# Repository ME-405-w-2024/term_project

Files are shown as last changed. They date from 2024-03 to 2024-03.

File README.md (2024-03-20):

# Term Project for ME405 at California Polytechnic University

## Contributors: Kevin Jung, Aidan Schwing, Noah Fitzgerald

Documentation available at: https://me-405-w-2024.github.io/term_project/

---

## Introduction
The code and CAD files present in this repository serve as reference for a fixed position, single-axis mechanism intended to shoot NERF RIVAL balls of approximately 1" diameter. This robot participated in a duel-style competition where two teams with similarly designed mechanisms competed to shoot the opposing team as quickly as possible. Robots were required to begin facing backwards, rotate 180 degrees, target with a thermal camera, and shoot the opponent.

Our team designed a custom shooting mechanism and implemented a stepper motor as our rotating axis. The specific implementation was intended for use by students in Cal Poly's ME 405 course, though use in the future is not limited to those individuals. Files are provided under the MIT License.  

While the documentation provided here may provide a good baseline, it is *not* comprehensive and *is not* intended to provide step-by-step instructions for recreation. 

## Hardware Overview
Much of the mechanical design was based on COTS hardware and components available on-hand. Shooting is performed with a [BLDC motor](https://hobbyking.com/en_us/propdrive-v2-2836-1800kv-brushless-outrunner-motor.html?wrh_pdp=3) driven by an [ESC](https://www.rcelectricparts.com/40a-esc---classic-series.html) and was sized to shoot at approximately the same speed as a stock NERF rifle. Balls are pushed into the wheels with a MG90s servo.

CAD images:

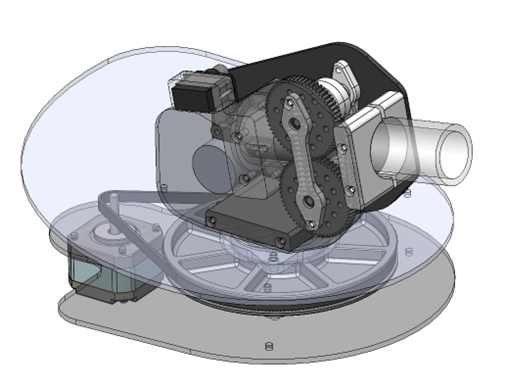
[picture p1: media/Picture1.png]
para front

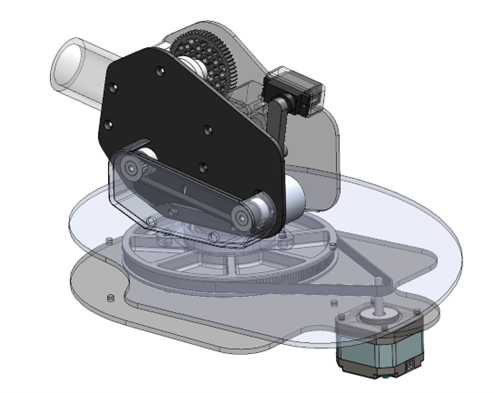
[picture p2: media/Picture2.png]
para rear

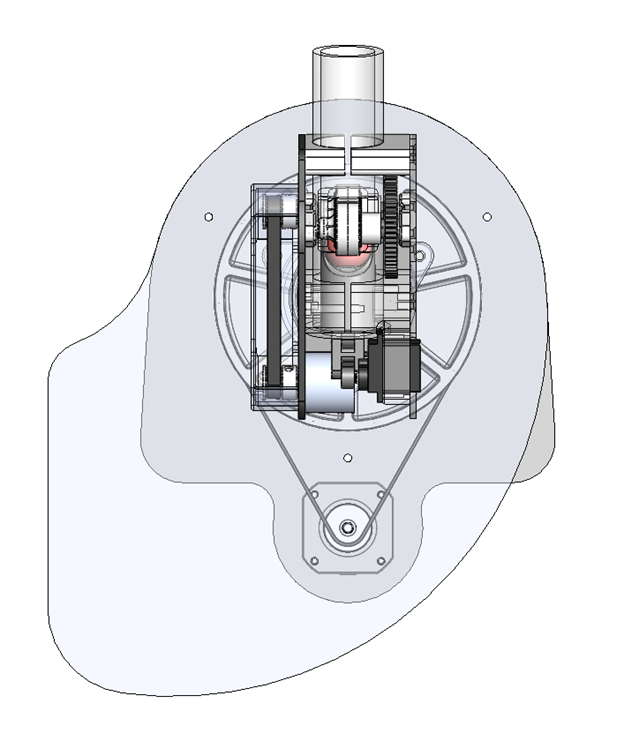
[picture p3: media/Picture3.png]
top view

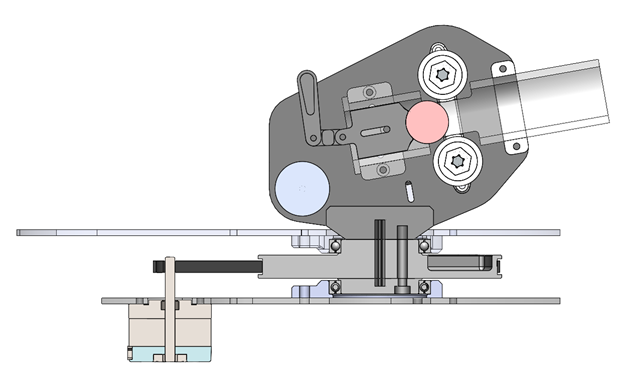
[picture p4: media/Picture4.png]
side section


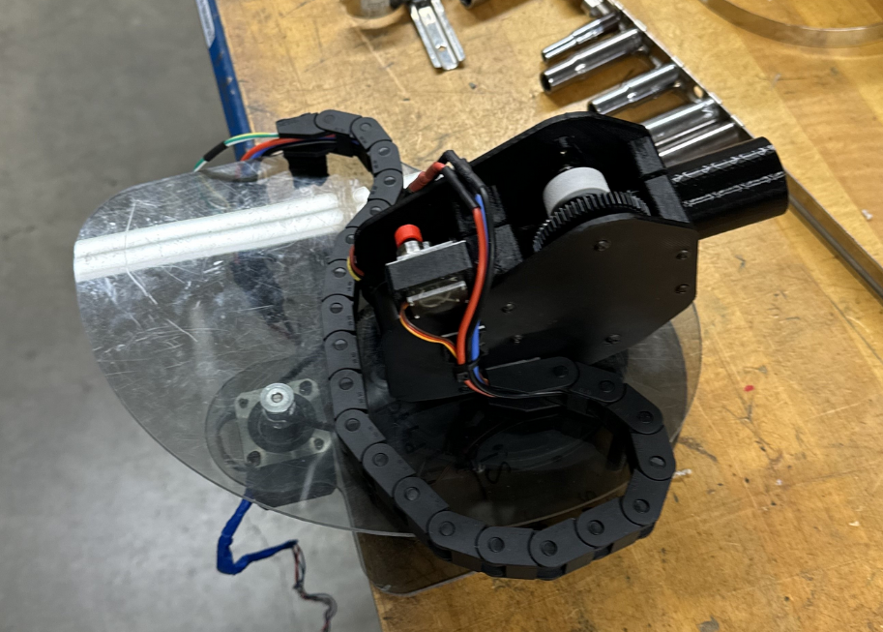
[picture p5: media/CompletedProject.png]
completed project


## Firmware Design

The firmware for the project was split across two microcontrollers. One handled only stepper motor control via a real-time planning method and received commands from the main controller over I2C. The other contained the main control loop and aiming algorithm, as well as control for PWM based devices such as the servo and the ESC.

Further information can be found in the [firmware specific documentation](https://me-405-w-2024.github.io/term_project/).

## Electrical Design
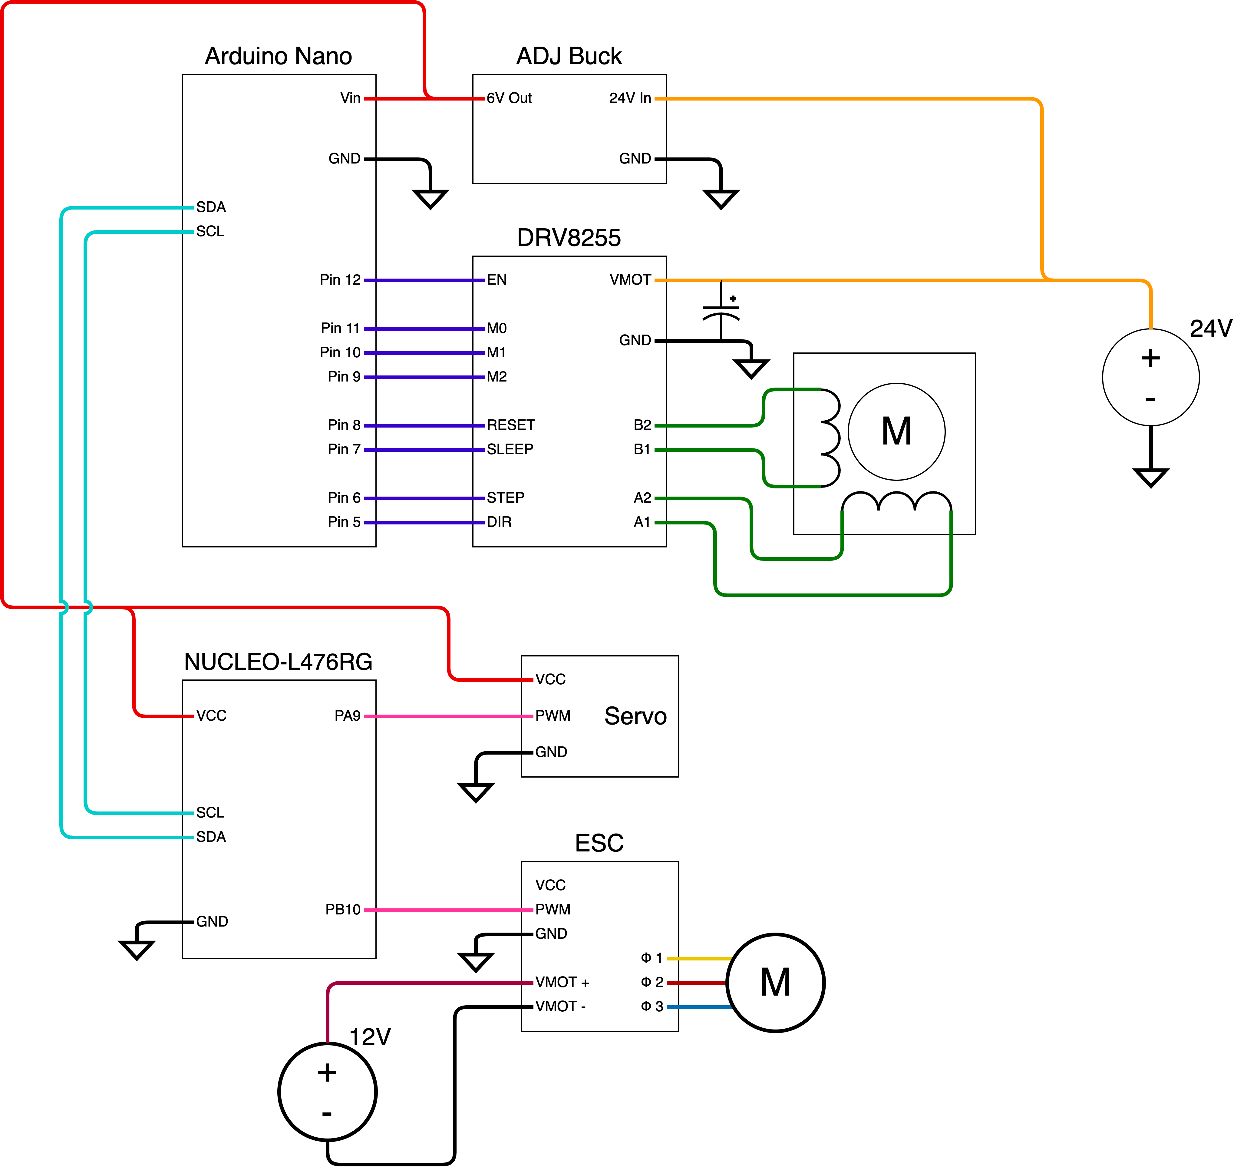
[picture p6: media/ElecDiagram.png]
schematic


## Results
The system was tested in multiple stages as mechanical hardware and the respective code implementations were completed. Almost all of the mechanical hardware was 3D printed before final implementation.

Shooting for this system was moderately successful. Our biggest issues were motor power consumption, shaft misalignment, and belt tension. Shooting performance was heavily dependent on available power supplied to the shooting motor and on ball compression, which was a function of shaft alignment and shooter wheel size. Shooting was tested off of the main pivot mechanism. Due to the speed of wheel rotation, belt tension was essential to ensuring functionality. 3D printed bearing mounts and mounting plates were iterated multiple times before the final design. 

Turning the shooter with a stepper motor proved to be challenging but successful. Mechanical design was fairly simple and integration was a matter of ensuring proper belt tension. Significant design work was put into the project to minimize rotational inertia, allowing for fast stepper accelerations. The turning system was tested using a routine of a few set angles, input angles were given to the system and performance was measured. 

Unfortunately the system did not perform flawlessly in competition. Much of the failure in competition was due to relatively low-complexity thermal data processing. A simple filter was implemented to attempt to pick up only significant hot-spots in thermal data, which proved to be a flawed approach and was heavily dependent on outside factors such as more than a single individual in view of the camera. We also used a USB cable to extend the I2C bus to the thermal camera, which meant that SCL and SDA lines were twisted, introducing more noise into the system.

## Lessons Learned
Implementation of a custom shooting mechanism proved to be quite challenging indeed. Much of the hardware was iterated at least 3 separate times before being deemed successful. 

The servo-based feed mechanism was remarkably successful due to the prevalence of robust servo hardware and ease of code implementation. The rotation-to-linear motion linkage proved highly reliable. 

Shaft alignment, concentricity, and belt tension proved the most challenging aspects of mechanical design. Proper belt tension provisions must be taken and rotating components should fit as tight as possible to any shafts to prevent excess losses. 

Ultimately, system integration proved to be the biggest challenge for this project. Each of the individual mechanical subsystems proved successful independently, but integration with the final thermal camera was the downfall of performance. More time should have been put into thermal camera data processing to accurately determine the centroid of heat for proper targeting, and less time should have been spent on mechanical hardware design. It did look cool, though. 

We recommend that this project is not recreated for similar competitions without significantly more time invested into entire system performance analysis. While the turning and shooting mechanisms proved interesting to design and program, the project did not perform better than a simple Nerf gun and required significantly more overhead for design and testing to even acquire baseline functionality.

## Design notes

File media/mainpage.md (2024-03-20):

# Overview

## Description of code

The code is broken up into three main portions, the main control loop, the camera processing functions, and the remote stepper driver.

### Main Control Loop

The main control loop is contained in main.py. It initalizes all neccesary objects and local variables in order to run all of the functions of the launcher.

This includes:

- Camera Driver
- Servo Driver
- Stepper Driver Communication
- Button Polling
- State Control

as the main functions.

As for the sequence of events controlled by the main loop, the operation is given below. This is also reflected in the state diagram.

1. Wait for button to be pressed.
2. Begin continuous targeting using the camera data, which is used to yield a target angle.
3. After 4 seconds of continuous targeting, the flywheels are spun up.
4. After 1 second of spinup, the targeted position is held for 1 more second.
5. After this time, the ball-indexing servo is moved to fire the ball.
6. Another 1 second delay is given to allow the flywheels time to slow down.
7. The turret returns to its home position and waits for another button press.

No tasks were used, as all time-sensitive functions were either handled by timer interrupts (in the cases where PWM was needed), or were handled on separate controllers (in the case of the stepper driver)

### Remote Stepper Driver

The aiming platform is a turret-based system that is rotated by a belt-driven stepper motor.

To achieve full control over the stepper motor's motion profile, a separate microcontroller is used as a dedicated step planner and generator. The controller used was an arduino nano with firmware written in both standard C++ as well as Arduino's version of C in order to leverage the ease of use from the arduino ecosystem.

This system relies heavily on accurate timing and low calculation overhead in order to achieve maximum step speed and accuracy. Additionally, motion planning was important in order to utilize the maximum speed of the stepper motor without losing steps. To accomplish these goals, a version of the [stepper control algorithm as laid out by D. Austin](https://cdck-file-uploads-europe1.s3.dualstack.eu-west-1.amazonaws.com/arduino/original/3X/f/7/f7861c732d17db124bdc320398a31bc2023ce996.pdf) was implemented. The only notable change made to the math was a conversion to units of RPM from rad/sec. More information on using individual functions can be found in StepperDriver.

The remote board (containing its own stepper driving hardware, the arduino, and power conversion) was communicated with via I2C, and given information of requested position, motor speed and motor accelerations. All other calculation was handled by the microcontroller on the arduino, freeing up significant time on the STM32.

## State Diagram

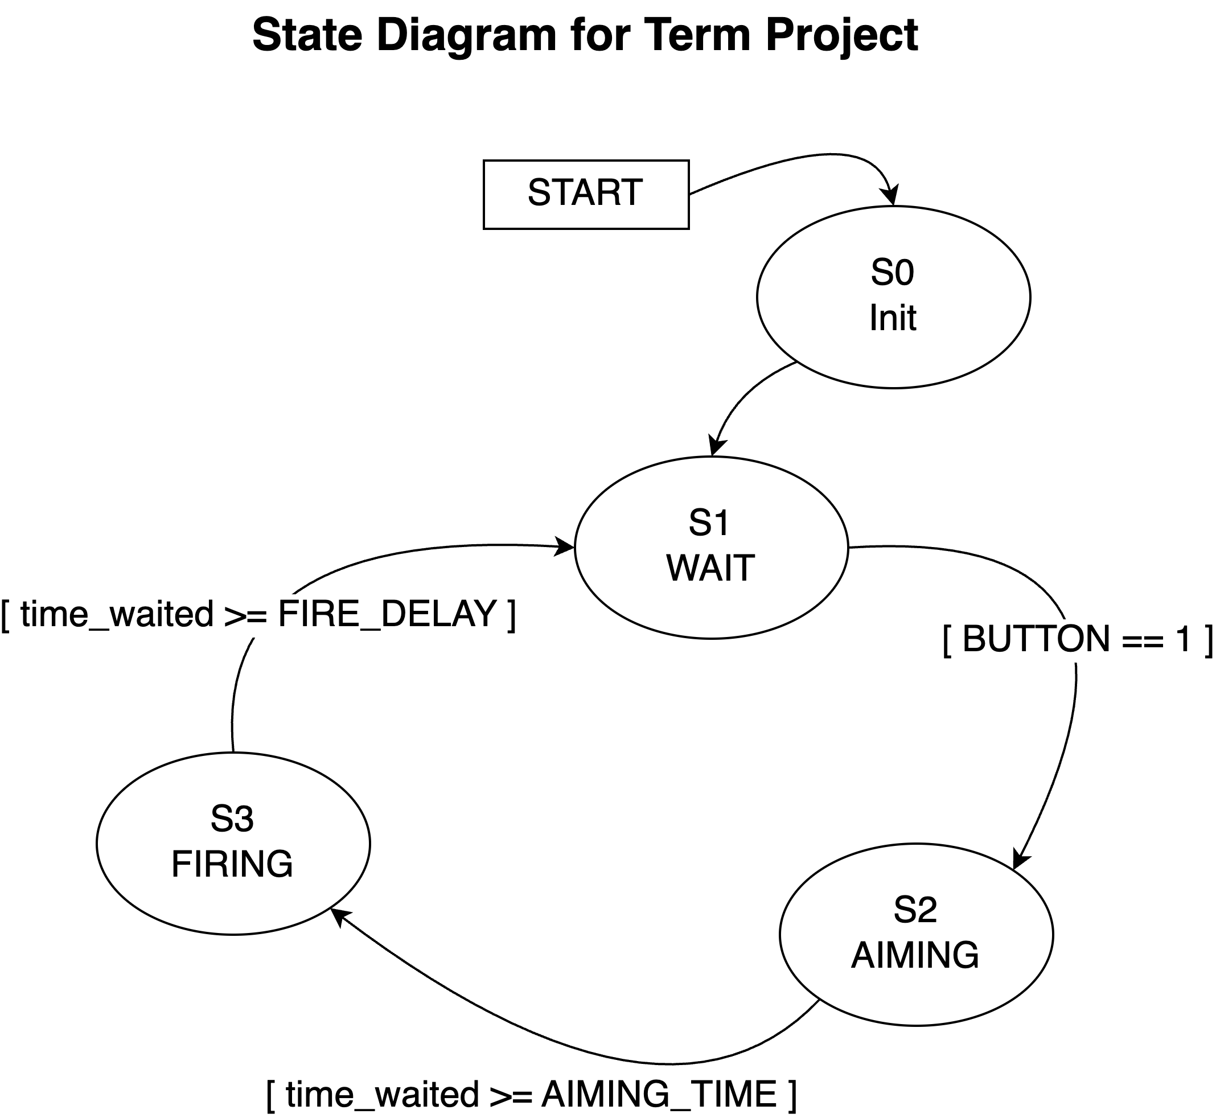
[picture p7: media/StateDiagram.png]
State Diagram


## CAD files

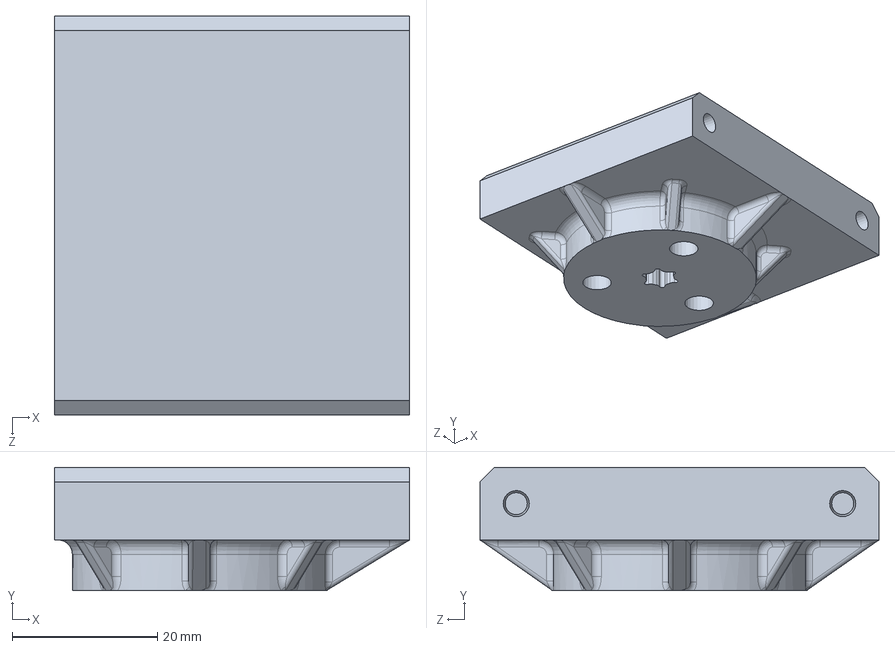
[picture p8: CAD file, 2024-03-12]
cad/main_body.SLDPRT
49.0 x 17.0 x 55.0 mm

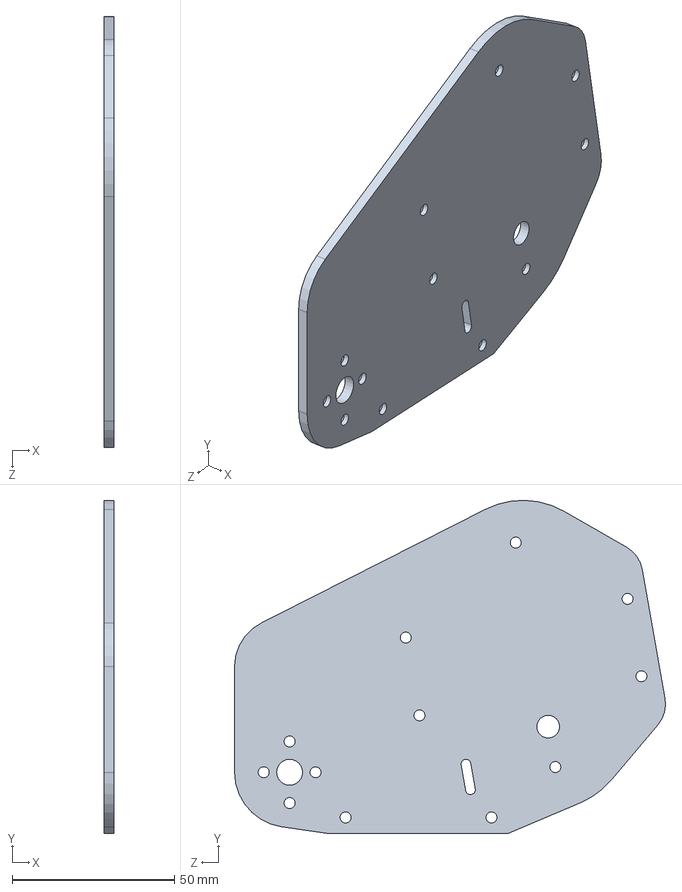
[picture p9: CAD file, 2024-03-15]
cad/side_panel_L.SLDPRT
3.00 x 102.8 x 132.9 mm

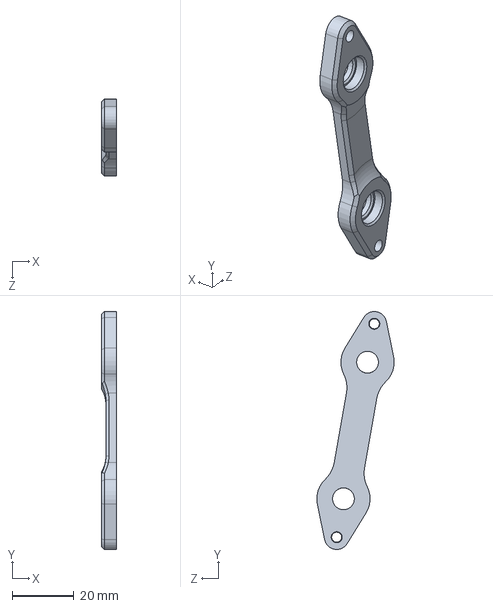
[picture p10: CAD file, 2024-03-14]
cad/mini_bearing_block.SLDPRT
5.00 x 77.2 x 25.1 mm

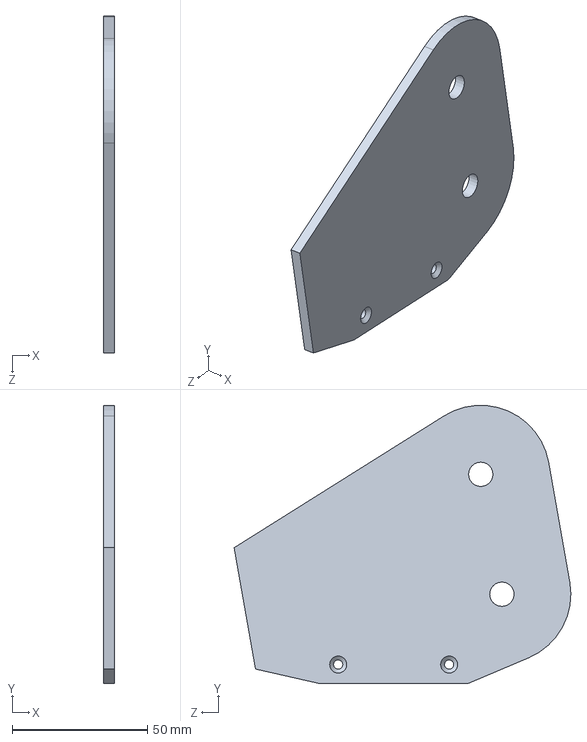
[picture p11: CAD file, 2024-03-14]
cad/side_panel_R.SLDPRT
4.00 x 102.8 x 124.5 mm

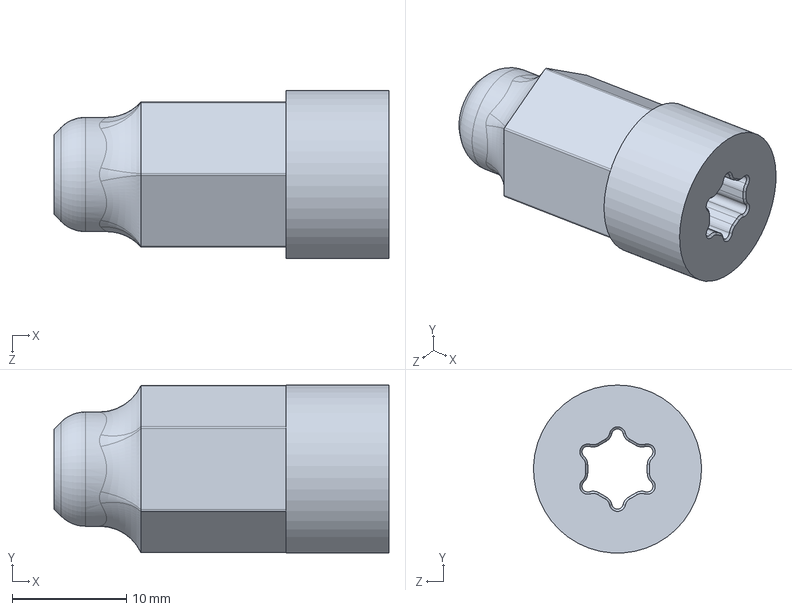
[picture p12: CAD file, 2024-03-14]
cad/hex_adapter.SLDPRT
29.3 x 14.7 x 14.7 mm

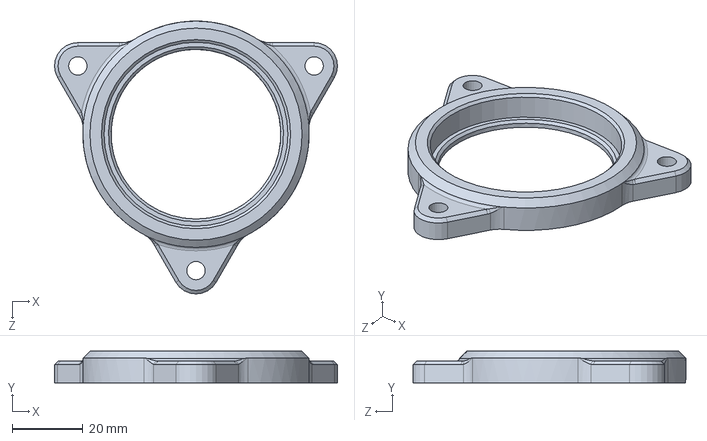
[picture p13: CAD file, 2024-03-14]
cad/42mm_bearing_block.SLDPRT
80.1 x 9.00 x 77.2 mm

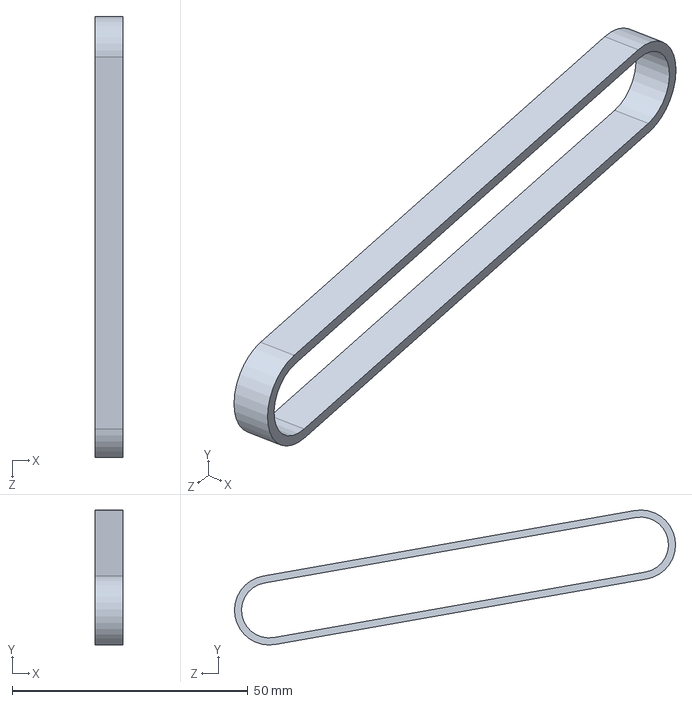
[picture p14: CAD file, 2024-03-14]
cad/Shooter Belt.SLDPRT
6.00 x 28.6 x 93.5 mm

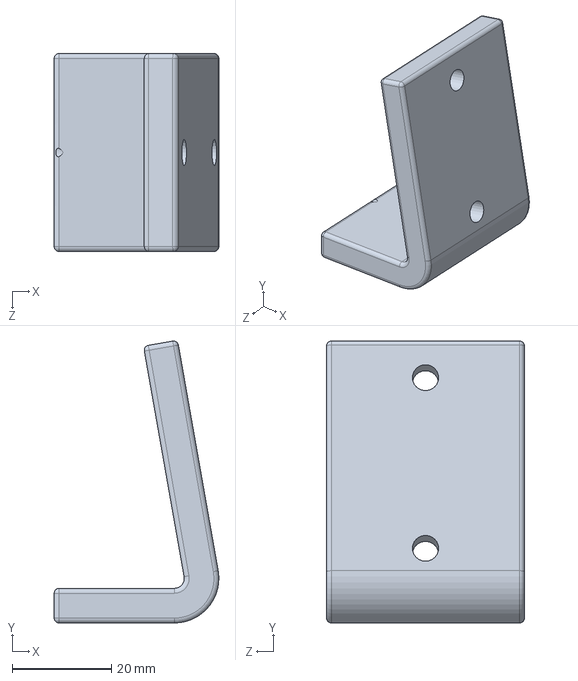
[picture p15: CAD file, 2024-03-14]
cad/CAMERA_MOUNT.SLDPRT
33.3 x 57.0 x 40.0 mm

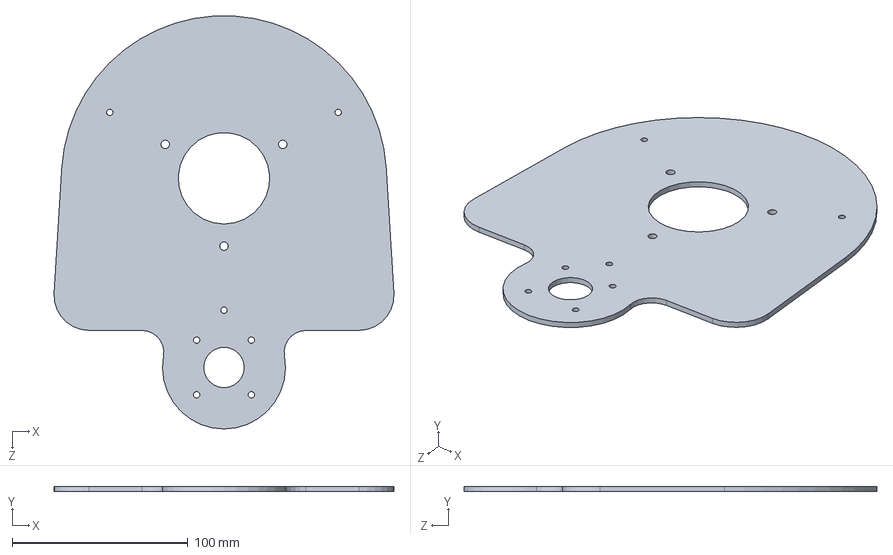
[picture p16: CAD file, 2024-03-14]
cad/bottom_plate.SLDPRT
193.4 x 3.00 x 234.9 mm

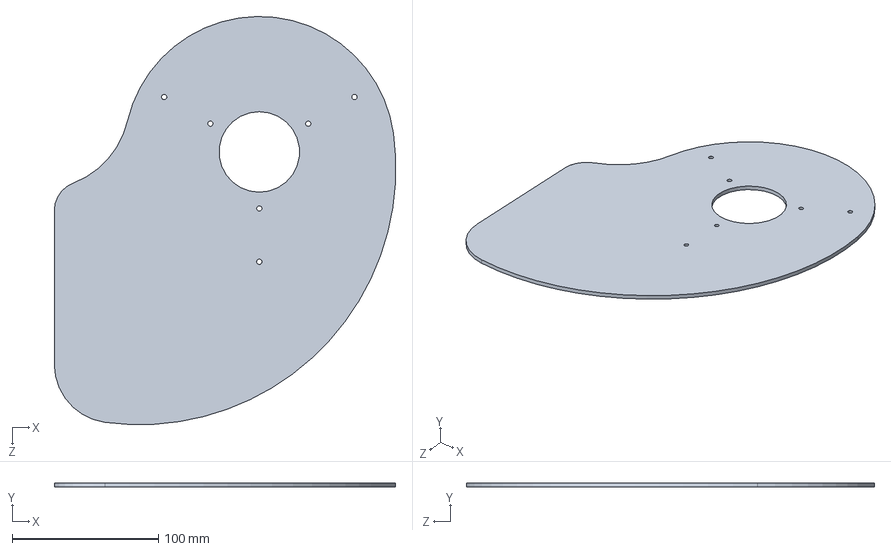
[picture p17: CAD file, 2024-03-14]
cad/top_plate.SLDPRT
233.1 x 3.00 x 278.6 mm

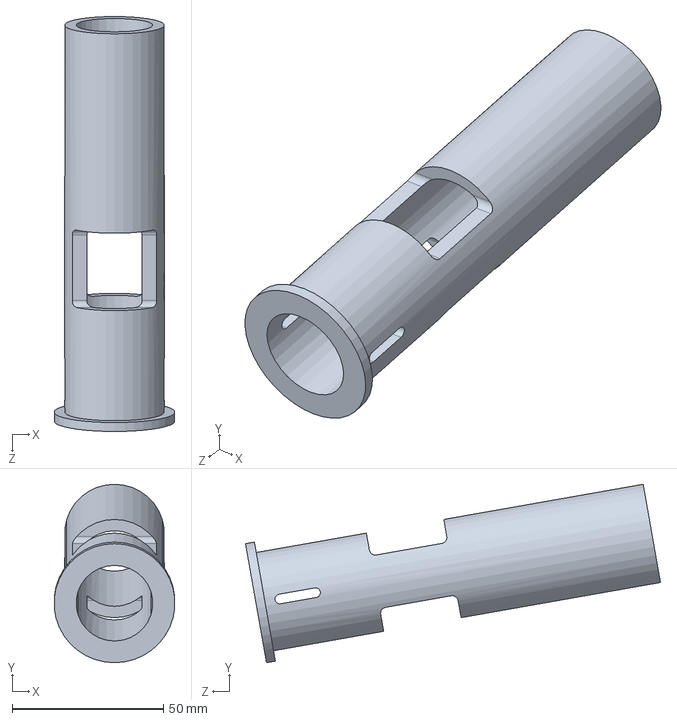
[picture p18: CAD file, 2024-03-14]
cad/shooter_tube.SLDPRT
39.9 x 59.0 x 137.3 mm

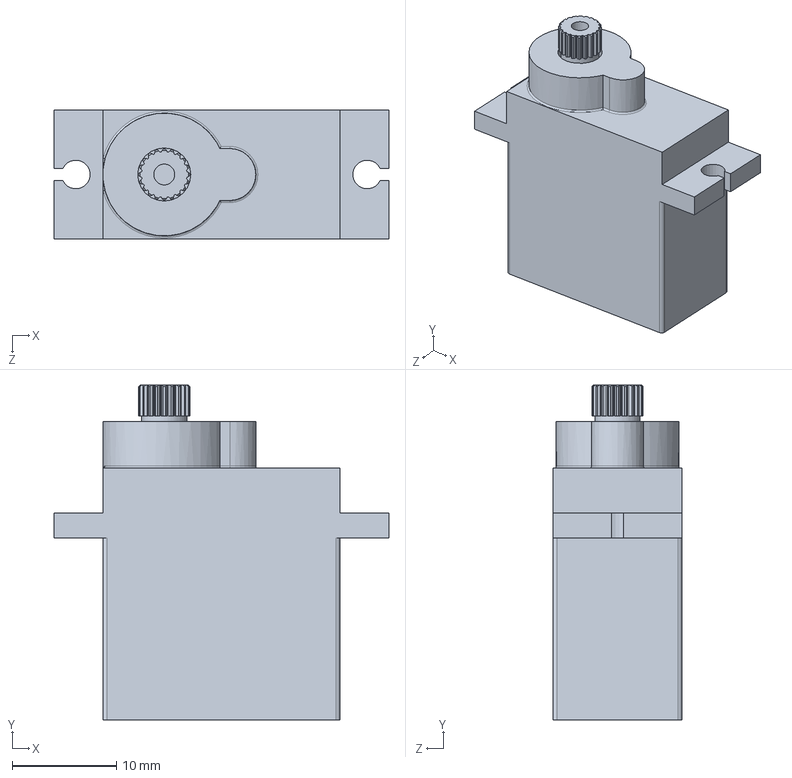
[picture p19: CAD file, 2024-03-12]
cad/MG90S Servo Motor.SLDPRT
32.2 x 32.2 x 12.4 mm

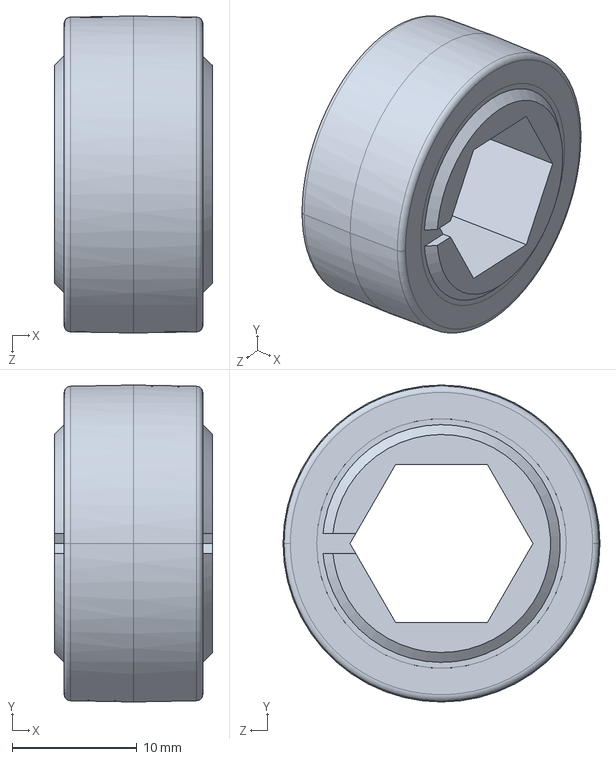
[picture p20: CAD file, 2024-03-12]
cad/REV-21-2048.SLDPRT
12.7 x 25.4 x 25.4 mm

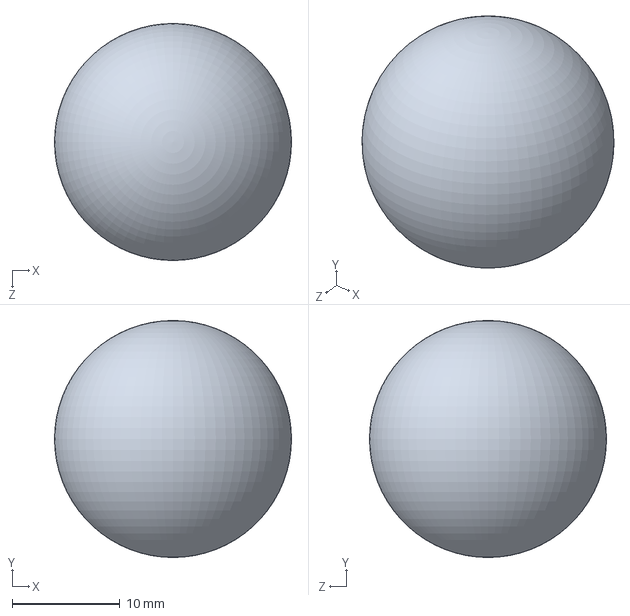
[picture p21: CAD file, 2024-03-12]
cad/ball.SLDPRT
22.0 x 22.0 x 22.0 mm

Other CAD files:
cad/detail_sketches_new.SLDPRT
cad/tube_clamp_front.SLDPRT
cad/GT2_20T.SLDPRT
cad/ball-holder.SLDPRT
cad/4668K271_Permanently Lubricated Stainless Steel Ball Bearing.SLDPRT
cad/6627T65_Stepper Motor.SLDPRT
cad/MR84-2RS Bearing.SLDPRT
cad/am-4541 Sushi Roller 500 Hex Bore.SLDPRT
cad/detail_sketches.SLDPRT
cad/drawing.SLDDRW
cad/hex_shaft.SLDPRT
cad/hex_shaft_extended.SLDDRW
cad/hex_shaft_extended.SLDPRT
cad/motor.SLDPRT
cad/pusher.SLDPRT
cad/servo arm.SLDPRT
cad/servo joint.SLDPRT
cad/sh-04215-016 solenoid electrified.SLDPRT
cad/shooter_tube.SLDDRW
cad/system_sketch.SLDPRT
cad/tube_clamp.SLDPRT

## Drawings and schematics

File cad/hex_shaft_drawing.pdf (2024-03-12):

B B

4

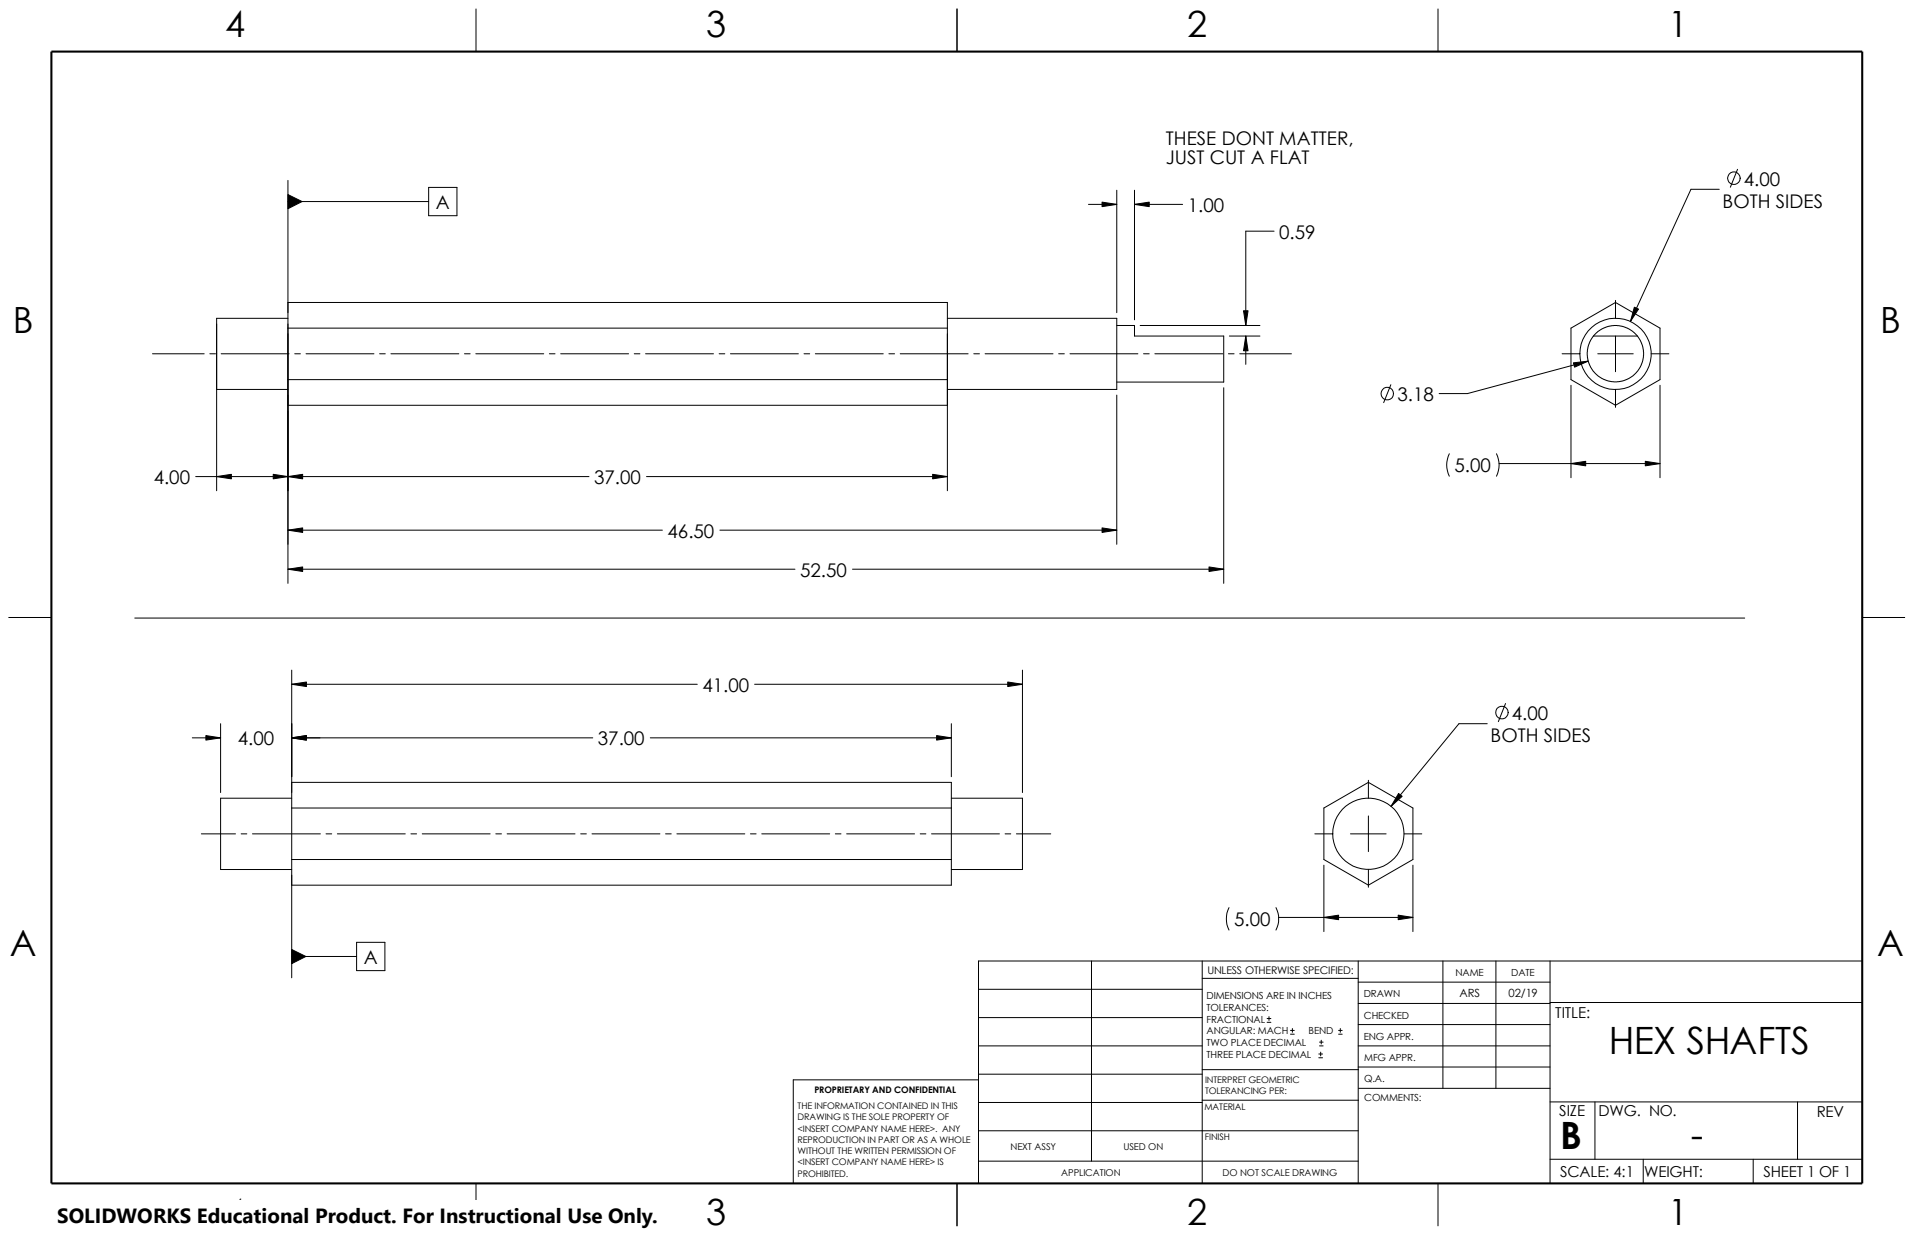
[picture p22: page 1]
COMMENTS:; 4.00 BOTH SIDES

THESE DONT MATTER,
JUST CUT A FLAT

UNLESS OTHERWISE SPECIFIED: | | NAME | DATE
DIMENSIONS ARE IN INCHES TOLERANCES: FRACTIONAL ANGULAR: MACH BEND TWO PLACE DECIMAL THREE PLACE DECIMAL | DRAWN | ARS | 02/19

CHECKED | | | TITLE: HEX SHAFTS

ENG APPR.
MFG APPR.

INTERPRET GEOMETRIC TOLERANCING PER: | Q.A.
MATERIAL | | SIZE B | DWG. NO. - | REV

PROPRIETARY AND CONFIDENTIAL
THE INFORMATION CONTAINED IN THIS
DRAWING IS THE SOLE PROPERTY OF
<INSERT COMPANY NAME HERE>. ANY
REPRODUCTION IN PART OR AS A WHOLE
WITHOUT THE WRITTEN PERMISSION OF
<INSERT COMPANY NAME HERE> IS
PROHIBITED.

NEXT ASSY | USED ON | FINISH

APPLICATION | DO NOT SCALE DRAWING | | SCALE: 4:1 | WEIGHT: | SHEET 1 OF 1

SOLIDWORKS Educational Product. For Instructional Use Only.

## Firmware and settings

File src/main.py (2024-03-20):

"""! @file main.py

This file lays out the main functionality of the shooting mechanism. 

"""  

import cotask
import task_share
import pyb
import globaldefs
import platform
import utime as time
import servo_driver
import micropython
from machine import I2C
from mlx_cam import MLX_Cam
from thermal_cam_processing import ThCamCalc

if "MicroPython" not in platform.platform():
    from me405_support import cotask, cqueue, task_share



micropython.alloc_emergency_exception_buf(100)


def rpm_to_rad_s(rpm):
    """! 
        Converts a RPM value to a Rad/Sec value
        @param rpm The input rpm to convert
        @returns The rotational speed in Rad/Sec
    """  
    return int(rpm/9.5493)


def percent_to_pwm(input, max_pwm, min_pwm):

    """! 
        Converts a standard 0-100 input to a PWM percent value based on given limits
        @param input The input percentage as a 0-100 value
        @param max_pwm The maximum PWM output corresponding to 100%
        @param min_pwm The minimum PWM output corresponding to 0%
        @returns The PWM percent pertaining to the input
    """  

    pwm_range = max_pwm-min_pwm

    pwm_percent = min_pwm + (pwm_range*input)

    return pwm_percent



if __name__ == "__main__":

    ##Pin object for the input button which starts the duel sequence
    button_pin = pyb.Pin(globaldefs.ONBOARD_BUTTON_PIN, pyb.Pin.IN, pull=pyb.Pin.PULL_UP)

    ##I2C object to communicate with the stepper driver controller
    stepper_i2c = pyb.I2C(1, pyb.I2C.CONTROLLER, baudrate=400000)


    
    # initialize thermal camera
    ##I2C object to communicate with the MLX camera
    cam_i2c = I2C(3, freq=3000000)
    ##MLX Camera object 
    therm_cam = MLX_Cam(cam_i2c)
    ##Thermal camera calculator object for returning useful targeting information
    therm_cam_calc = ThCamCalc(DIST_CAM=globaldefs.CAMERA_TARGET_DIST_IN,
                               DIST_SHOOTER=globaldefs.SHOOTER_TARGET_DIST_IN,
                               FOV_ANG=globaldefs.CAM_FOV_DEG,
                               NUM_PIXELS=globaldefs.CAM_X_PIXELS)

    

    ##Object to control the servo used to initiate firing
    ball_servo = servo_driver.ServoDriver(pwm_pin=globaldefs.SERVO_PWM_PIN, 
                                          pwm_timer_num=globaldefs.SERVO_PWM_PIN_TIMER_NUM,
                                          pwm_channel_num=globaldefs.SERVO_PWM_PIN_TIMER_CHANNEL,
                                          pwm_max_pulse=globaldefs.SERVO_MAX_PWM_US,
                                          pwm_min_pulse=globaldefs.SERVO_MIN_PWM_US,
                                          full_angle_range=globaldefs.SERVO_ANGLE_RANGE,
                                          period_ARR=globaldefs.SERVO_TIMER_ARR,
                                          period_PS=globaldefs.SERVO_TIMER_PS)

    ##Pin object to define the pin to be used for PWM control of the flywheel motor
    flywheel_motor_pwm_pin = pyb.Pin(globaldefs.FLYWHEEL_MOTOR_PWM_PIN, pyb.Pin.OUT_PP)
    ##Timer object for PWM control of the flywheel motor
    flywheel_motor_pwm_timer = pyb.Timer(globaldefs.FLYWHEEL_MOTOR_PWM_PIN_TIMER_NUM, freq=globaldefs.FLYWHEEL_MOTOR_PWM_FREQUENCY)
    ##Timer channel object for PWM control of the flywheel motor
    flywheel_motor_pwm_timer_channel= flywheel_motor_pwm_timer.channel(globaldefs.FLYWHEEL_MOTOR_PWM_PIN_TIMER_CHANNEL, pyb.Timer.PWM, pin=flywheel_motor_pwm_pin)

    ##Value of the PWM to be sent to the ESC to control the flywheel motor
    flywheel_pwm_value = percent_to_pwm(0, globaldefs.FLYWHEEL_MOTOR_MAX_PWM, globaldefs.FLYWHEEL_MOTOR_MIN_PWM)
    flywheel_motor_pwm_timer_channel.pulse_width_percent(flywheel_pwm_value)

    ball_servo.set_angle(180)

    ##Target speed of the rotation of the stepper motor in RPM
    target_rotation_speed = 10000
    ##Target acceleration of the stepper motor in (RPM/s)/10
    rotation_acceleration = 9000
    ##Target deceleration of the stepper motor in (RPM/s)/10
    rotation_deceleration = 9000
    ##Target position for the stepper motor to rotate to in deg
    pivot_target_deg = int(180*globaldefs.PULLEY_RATIO)

    ##Delay in ms to do pure targeting before switching to firing
    fire_delay = 4000

    ##The current position of the stepper motor in deg
    current_pos = 0

    ##The last position of the stepper motor in deg
    last_angle = 0

    ##The next/current position of the stepper motor in deg
    next_angle = 0

    ##Initial time at which the duel activation button was pressed
    press_time = 0

    ##Flag to determine if the motor is in an active duel/targeting 
    active = 0



    try:

        while 1:

            if(button_pin.value()==0):

                print("Start")

                press_time = time.ticks_ms()

                last_angle = 0

                current_pos = 0

                next_angle = 0

                active = 1
                

            if (active == 1):

                last_angle = next_angle

                ##The current detected centroid location
                centroid = therm_cam_calc.get_centroid(therm_cam)/10

                next_angle = therm_cam_calc.get_angle(centroid)

                next_angle = next_angle + globaldefs.CAM_TARGET_ANGLE_OFFSET

                ##The angle change between the last stepper angle and the next target angle
                angle_delta = (next_angle-last_angle)

                current_pos += angle_delta

                pivot_target_deg = int(angle_delta * globaldefs.PULLEY_RATIO)


                #Rotation start
                ##Data to send to the stepper controller
                buffer = bytearray([pivot_target_deg>>8, pivot_target_deg, 
                                    target_rotation_speed>>8, target_rotation_speed,
                                    rotation_acceleration>>8, rotation_acceleration,
                                    rotation_deceleration>>8, rotation_deceleration])

                stepper_i2c.send(buffer, globaldefs.STEPPER_I2C_ADDR)
                

                print(f"Targeting at: {angle_delta}, from centroid {centroid}")

                if((time.ticks_ms() - press_time) > fire_delay):

                    #Spin flywheel
                    flywheel_pwm_value = percent_to_pwm(0.2, globaldefs.FLYWHEEL_MOTOR_MAX_PWM, globaldefs.FLYWHEEL_MOTOR_MIN_PWM)
                    flywheel_motor_pwm_timer_channel.pulse_width_percent(flywheel_pwm_value)


                    #Delay to ensure flywheel spinup
                    time.sleep(1)

                    #Rotation start
                    buffer = bytearray([pivot_target_deg>>8, pivot_target_deg, 
                                        target_rotation_speed>>8, target_rotation_speed,
                                        rotation_acceleration>>8, rotation_acceleration,
                                        rotation_deceleration>>8, rotation_deceleration])

                    stepper_i2c.send(buffer, globaldefs.STEPPER_I2C_ADDR)
                    
                    #Delay to complete rotation
                    time.sleep(1)

                    #Fire ball
                    ball_servo.set_angle(180-30)

                    #Delay to ensure full speed when ball fired
                    time.sleep(0.25)

                    #Flywheel spindown
                    ball_servo.set_angle(180)
                    
                    flywheel_pwm_value = percent_to_pwm(0, globaldefs.FLYWHEEL_MOTOR_MAX_PWM, globaldefs.FLYWHEEL_MOTOR_MIN_PWM)
                    flywheel_motor_pwm_timer_channel.pulse_width_percent(flywheel_pwm_value)


                    #Delay to return to home when safe
                    time.sleep(1)

                    pivot_target_deg = int(current_pos * globaldefs.PULLEY_RATIO)

                    buffer = bytearray([(-1*pivot_target_deg)>>8, (-1*pivot_target_deg), 
                                        target_rotation_speed>>8, target_rotation_speed,
                                        rotation_acceleration>>8, rotation_acceleration,
                                        rotation_deceleration>>8, rotation_deceleration])
                    
                    stepper_i2c.send(buffer, globaldefs.STEPPER_I2C_ADDR)
                    
                    active = 0

                


    except KeyboardInterrupt:

        flywheel_pwm_value = percent_to_pwm(0, globaldefs.FLYWHEEL_MOTOR_MAX_PWM, globaldefs.FLYWHEEL_MOTOR_MIN_PWM)
        flywheel_motor_pwm_timer_channel.pulse_width_percent(flywheel_pwm_value)
        flywheel_motor_pwm_timer.deinit() 

        ball_servo.set_angle(180)
        ball_servo.disable_stepper()

        print("Exit")

        time.sleep(0.1)
        
    

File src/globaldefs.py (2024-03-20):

"""! @file globaldefs.py

Serves as an outline of constants that are used multiple times throughout the code.
Pin definitions for GPIO are defined here to provide a central source of truth. 

"""  

import pyb

##I2C address of the stepper controller
STEPPER_I2C_ADDR = 105

##Pin of the PWM input for the flywheel motor ESC
FLYWHEEL_MOTOR_PWM_PIN = pyb.Pin.board.PB10
##Timer number corresponding to the ESC pwm pin
FLYWHEEL_MOTOR_PWM_PIN_TIMER_NUM = 2
##Timer channel number corresponding to the ESC pwm pin
FLYWHEEL_MOTOR_PWM_PIN_TIMER_CHANNEL = 3

##Frequency of the PWM signal for the ESC
FLYWHEEL_MOTOR_PWM_FREQUENCY = 50

##PWM percentage for max speed on the ESC
FLYWHEEL_MOTOR_MAX_PWM = 10
##PWM percentage for min speed on the ESC
FLYWHEEL_MOTOR_MIN_PWM = 5

##Max integer value of the internal adc
ADC_MAX_INTEGER = 4095

##Pin location of the onboard blue button
ONBOARD_BUTTON_PIN = pyb.Pin.board.PC13

##Distance in inches from the target to the camera
CAMERA_TARGET_DIST_IN = 200#192
##Distance in inches from the target to the turret/launcher
SHOOTER_TARGET_DIST_IN = 300#192-60-30
##FOV of the camera in degrees
CAM_FOV_DEG = 55
##Pixels in the horizontal direction for the camera
CAM_X_PIXELS = 32

##Calibration offset for camera aiming
CAM_TARGET_ANGLE_OFFSET = 0

##Ratio of the rotation motor to the actual turret
PULLEY_RATIO = 9.5

##Pin of the PWM input for servo position control
SERVO_PWM_PIN = pyb.Pin.board.PA9
##Timer number corresponding to the servo PWM pin
SERVO_PWM_PIN_TIMER_NUM = 1
##Timer channel number corresponding to the servo PWM pin
SERVO_PWM_PIN_TIMER_CHANNEL = 2

# constants to set servo freq to 50hz w/ tick int of 1us
##Auto-reset value for the servo PWM generator
SERVO_TIMER_ARR = 19999
##Timer prescaler for the servo PWM generator
SERVO_TIMER_PS = 79

##Pulse width corresponding to the maximum position of the servo
SERVO_MAX_PWM_US = 2600
##Pulse width corresponding to the minimum position of the servo
SERVO_MIN_PWM_US = 600
##Range of motion for the servo
SERVO_ANGLE_RANGE = 180

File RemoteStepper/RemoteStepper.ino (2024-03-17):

// @file RemoteStepper.ino

#include <Wire.h>
#include "StepperFunctions.h"
#include "TimerFunctions.h"

int currentState = 0;
int lastState = 0;

int potValScaled = 0;
int lastVal = 0;
int speedSet = 300;
int inputPos = 90*3;

int calcTicks = 0;
long delayTicks = 0;

long nextDelayTicks = 0;

byte DDRDstate = 0;
byte PORTDstate = 0;
byte DDRBstate = 0;
byte PORTBstate = 0;
byte DDRCstate = 0;
byte PORTCstate = 0;

long toop = 0;

long nextActionTicks = 0;
long interruptElapsedTicks = 0;


bool receive_flag = false;


StepperDriver stepper0;


int16_t requested_pivot_target_deg = 0;
uint32_t requested_acceleration = 0;
uint32_t requested_deceleration = 0;
uint32_t requested_rotation_speed = 0;


int posState = 0;
int step1PosTarget = 360;

int currentAcccel = 0;
int currentDecel = 0;
int currentSpeed = 0;

void setup() {
  Serial.begin(230400);

  Wire.begin(0x69);
  Wire.setClock(400000);

  Wire.onRequest(request_handler);

  Wire.onReceive(receive_handler);

  timer1Setup();
  timer1Enable();

  //(int microsteps, int stepPerRev, int stepPin, int dirPin, int M1, int M2, int M3, int enablePin)
  stepper0.setupStepper(1, 200, 6, 5, 11, 10, 9, 12);


  for (int i = 2; i <=  20; i++) {
    pinMode(i, OUTPUT);
  }

  digitalWrite(7,HIGH);
  digitalWrite(8,HIGH);

  //timer0Setup();
  //TIMER0_DISABLE();

  //100000
  stepper0.setAcceleration(50000);
  stepper0.setDeceleration(50000);

  //setArmRotation(500, 360);

  stepper0.enableStepper();
}

void loop() {

  if (stepper0.getState() == 0){
    stepper0.disableStepper();

    if(receive_flag == true){

      receive_flag = false;
      stepper0.setAcceleration(requested_acceleration);
      stepper0.setDeceleration(requested_deceleration);
      stepper0.changePos(requested_pivot_target_deg,requested_rotation_speed);
      nextDelayTicks = stepper0.calculateNextStep();
      start_timer();
      stepper0.enableStepper();

    }

  } else {
    stepper0.enableStepper();
  }

}

void start_timer(){
  TCNT1 = 0;
  OCR1A = 100;
  timer1Enable();
}


void request_handler(){

}

void receive_handler(int bytes){
  

  Serial.print("Received data length: ");
  Serial.println(bytes);

  if(bytes == 8){

    receive_flag = true;
    
    while(Wire.available()){
      requested_pivot_target_deg =  (int16_t) (Wire.read()<<8) + (Wire.read()); 
      requested_rotation_speed = ((uint32_t) (Wire.read()<<8) + (Wire.read())) * 10;
      requested_acceleration = ((uint32_t) (Wire.read()<<8) + (Wire.read())) * 10;
      requested_deceleration = ((uint32_t) (Wire.read()<<8) + (Wire.read())) * 10;
    }

  }

}

//ISR overhead of about 8us
ISR(TIMER1_COMPA_vect) {

  cli(); //Mask interrupt

  // DDRDstate = DDRD;
  // PORTDstate = PORTD;
  // DDRBstate = DDRB;
  // PORTBstate = PORTB;
  // DDRCstate = DDRC;
  // PORTCstate = PORTC;

  do{

  OCR1A = 65535; //set compare to max
  TCNT1 = 0; //Reset timer counter

  if(stepper0.getState() != 0){

    stepper0.fullStep();//Step

  }

  sei(); //unmask interrupt

  

  nextActionTicks = stepper0.calculateNextStep(); //Get ticks to next step

  // Serial.println(nextActionTicks);

  cli(); //mask interrupt
  interruptElapsedTicks = TCNT1; //Get how many ticks have elapsed while in the interrupt
  TCNT1 = 0; //reset timer
  
  nextDelayTicks = nextActionTicks-interruptElapsedTicks; //set next interrupt taking into account how much time this one has taken

  if(nextDelayTicks > 16){//Take in account the 8 us overhead
    OCR1A = nextDelayTicks;
  } else {
      //Serial.println("Fuk");
      //Serial.println();
  }

    // Serial.print(nextActionTicks);
    // Serial.print(" - ");
    // Serial.print(interruptElapsedTicks);
    // Serial.print(" = ");
    // Serial.println(nextDelayTicks);
    // Serial.println();

  } while(nextDelayTicks < 16); //Repeat if there is not enough time for leaving the interrupt


  // DDRD = DDRDstate;
  // PORTD = PORTDstate;
  // DDRB = DDRBstate;
  // PORTB = PORTBstate;
  // DDRC = DDRCstate;
  // PORTC = PORTCstate;

  sei(); //unmask interrupt
}

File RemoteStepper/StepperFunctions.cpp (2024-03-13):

#include "StepperFunctions.h"

  

    StepperDriver::StepperDriver() {
      currentState = ERROR;
    }


    void StepperDriver::setupStepper(int microsteps, int stepPerRev, int stepPin, int dirPin, int M1, int M2, int M3, int enablePin) {
      microSteps = microsteps;
      stepsPerRev = stepPerRev;
      stepperStepPin = stepPin;
      stepperDirPin = dirPin;
      stepperM1 = M1;
      stepperM2 = M2;
      stepperM3 = M3;
      stepperEnablePin = enablePin;

      disableStepper();

      currentState = STOP;

      int m1State = 0;
      int m2State = 0;
      int m3State = 0;

      switch (microsteps) {
        case 2:
          m1State = 1;
          break;

        case 4:
          m2State = 1;
          break;

        case 8:
          m1State = 1;
          m2State = 1;
          break;

        case 16:
          m1State = 1;
          m2State = 1;
          m3State = 1;
          break;
      }

      digitalWrite(stepperM1, m1State);
      digitalWrite(stepperM2, m2State);
      digitalWrite(stepperM3, m3State);

      
    }


    void StepperDriver::setStepperSpeed(int speed) {
      updateStepperSpeed(pulsesPerSecond(speed));
      timer1ChangeFrequency(pulsesPerSecond(speed) * 2, 8); //multipled by 2 because toggle
      timer1Enable();
    }

//    void setTargetSpeed(int RPM) {
//      targetSpeed = RPM;
//      targetDegPerSec = RPM * 6;
//      timer1Enable();
//      stopped = false;
//    }

    void StepperDriver::updateStepperSpeed(int speed) {
      targetSpeed = speed;
    }





    //Calculations
    int StepperDriver::pulsesPerSecond(int speed) {
      return ((long)speed * stepsPerRev * microSteps) / 360;
    }

    int StepperDriver::stepMicros(int speed) {
      return 1000000 / speed;
    }





    //Enable/Disable
    void StepperDriver::enableStepper() {
      digitalWrite(stepperEnablePin, 0);
    }

    void StepperDriver::disableStepper() {
      digitalWrite(stepperEnablePin, 1);
    }





    //Direction
    void StepperDriver::dirSetCW() {
      stepperDirection = 1;
      digitalWrite(stepperDirPin, HIGH);

      #ifdef DEBUG
      Serial.println("CW Direction");
      #endif
    }

    void StepperDriver::dirSetCCW() {
      stepperDirection = -1;
      digitalWrite(stepperDirPin, LOW);

      #ifdef DEBUG
      Serial.println("CCW Direction");
      #endif
    }

    int StepperDriver::getDir() {
      return stepperDirection;
    }





    //States
    stepperStates StepperDriver::getState(){
      return currentState;
    }






    //Positioning
    void StepperDriver::setPos(long posDegree, int speed) { //speed in deg/s

      timer1Disable();


      if(posDegree < getCurrentPosition()){
        dirSetCCW();   

      } else {
        dirSetCW();

      }

      posDelta = abs(getCurrentPosition() - posDegree);
      targetSpeed = pulsesPerSecond(speed); //outputs uSteps/s
      targetPulses = ((long)posDelta * stepsPerRev) / 360 * microSteps;

      calculateMoveProfile();

      //Set current state to acceleration
      currentState = ACCELERATE;

      enableStepper();

      #ifdef DEBUG
      Serial.print("currentPosition:");
      Serial.println(getCurrentPosition());
      Serial.print("posDelta:");
      Serial.println(posDelta);
      Serial.print("targetPulses:");
      Serial.println(targetPulses);
      Serial.print("Initial currentSpeedPulse: ");
      Serial.println(currentSpeedPulse);
      Serial.println();
      #endif



      //Set timer to delay and start timer
      // cli();
      // TCNT1 = 0;
      // OCR1A = currentSpeedPulse;
      // timer1Enable();
      // sei();
      

    }

    void StepperDriver::changePos(long posDegree, int speed) { //speed in deg/s

      timer1Disable();


      if(posDegree < 0){
        dirSetCCW();   

      } else {
        dirSetCW();

      }

      posDelta = abs(posDegree);
      targetSpeed = pulsesPerSecond(speed); //outputs uSteps/s
      targetPulses = ((long)posDelta * stepsPerRev) / 360 * microSteps;

      calculateMoveProfile();

      //Set current state to acceleration
      currentState = ACCELERATE;

      enableStepper();


      #ifdef DEBUG
      Serial.print("currentPosition:");
      Serial.println(getCurrentPosition());
      Serial.print("posDelta:");
      Serial.println(posDelta);
      Serial.print("targetPulses:");
      Serial.println(targetPulses);
      Serial.print("Initial currentSpeedPulse: ");
      Serial.println(currentSpeedPulse);
      Serial.println();
      #endif



      //Set timer to delay and start timer
      // cli();
      // TCNT1 = 0;
      // OCR1A = currentSpeedPulse;
      // timer1Enable();
      // sei();
      

    }

    long StepperDriver::getCurrentPosition() {
      return (totalSteps*360)/(stepsPerRev*microSteps);
    }

    void StepperDriver::resetPosition() {
      totalSteps = 0;
    }

    void StepperDriver::incrementPos(){
      totalSteps += stepperDirection;
    }






    //Stepping
    void StepperDriver::fullStep() {
      digitalWrite(stepperStepPin, HIGH);
      //PORTD = PORTD | 1 << (stepperStepPin);
      incrementPos();
      remainingSteps--;
      currentSteps++;
      digitalWrite(stepperStepPin, LOW);
      //PORTD = PORTD & 0 << (stepperStepPin);
    }

    void StepperDriver::setBrake() {
      if (currentState != STOP) {
        digitalWrite(stepperStepPin, LOW);
        currentState = STOP;
      }
      currentSpeedPulse = 65535;
      currentSpeed = 0;
      targetSpeed = 0;
    }





    void StepperDriver::setAcceleration(long accelDeg){ //input is deg/s^2
      accelVal = ((long)accelDeg*stepsPerRev*microSteps)/360; //output is uSteps/s^2
      #ifdef DEBUG
      Serial.print("accelVal: ");
      Serial.println(accelVal);
      #endif
    }

    void StepperDriver::setDeceleration(long decelDeg){
      decelVal = ((long)decelDeg*stepsPerRev*microSteps)/360;
    }

    long StepperDriver::getAcceleration(){
      return accelVal;
    }

    long StepperDriver::getDeceleration(){
      return decelVal;
    }

    void StepperDriver::calculateMoveProfile(){

        // speed is in [uSteps/s]
        // how many microsteps from 0 to target speed
        accelSteps = ( (long)targetSpeed * targetSpeed / ((long)2*accelVal) );
        // how many microsteps are needed from cruise speed to a full stop
        decelSteps = (long)accelSteps * accelVal / decelVal;

        if (targetPulses < accelSteps + decelSteps){
          // cannot reach max speed, will need to brake early
          accelSteps = (long)targetPulses * decelVal / ((long)accelVal + decelVal);
          decelSteps = (long)targetPulses - accelSteps;

        }

        decelStartStep = targetPulses - decelSteps;


        //Set remaining steps
        currentSteps = 0;
        remainingSteps = targetPulses;

        // Initial pulse (c0) including error correction factor 0.676 [us]
        currentSpeedPulse = -1 * (float) ((TIMER_CLOCK)*0.676) * sqrt(2.0/accelVal);

        pulseCalcRemainder = 0;
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

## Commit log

2024-02-11 Push cad
    bearing blocks and stuff
    [42mm_bearing_block.SLDPRT, 42mm_bearing_block.STL, 42mm_bearing_block2.STL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]
2024-02-12 tweaking stuff
    [detail_sketches.SLDPRT, main_body.SLDPRT, pusher.SLDPRT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]
2024-02-13 pushing more trash
    [MG90S Servo Motor.SLDPRT, ball.SLDPRT, detail_sketches.SLDPRT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]
2024-02-15 pwm stuff
2024-02-15 update to latest
    [MG90S Servo Motor.SLDPRT, ball-holder.SLDPRT, ball-holder.STL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]
2024-02-23 More servo
2024-02-29 updating cad
    [42mm_bearing_block.SLDPRT, 6627T65_Stepper Motor.SLDPRT, GT2_20T.SLDPRT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]
2024-03-07 Calibration for ESC
2024-03-08 added driver library and script for the thermal camera
    added basic code in main.py to allow for basic functionality of the camera.
2024-03-11 adding in angle calculation
    [main_pulley_bottom.STL, side_panel_R.STL]
2024-03-12 Added old arduino code
2024-03-13 Added arduino code and such
2024-03-14 changing to the nonblocking cam
    [42mm_bearing_block.SLDPRT, CAMERA_MOUNT.SLDPRT, Shooter Belt.SLDPRT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]
2024-03-15 un-destroy cad again again again
    [42mm_bearing_block.SLDPRT, 42mm_bearing_block.STL, 42mm_bearing_block2.STL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]
2024-03-18 Updated docs for arduino code
2024-03-20 updating readme and adding final code comments.
    [42mm_bearing_block.STL, 42mm_bearing_block2.STL, ball-holder.STL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]
